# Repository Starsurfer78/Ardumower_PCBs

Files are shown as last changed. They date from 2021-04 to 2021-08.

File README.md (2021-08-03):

DIY Robot Lawn Mower Community: https://www.diy-robot-lawn-mower.com/

# Simple Ardumower_PCBs

If you want to buy a Board, you can send me an E-Mail: info@projekt-heimwerken.de

# Simple MainPCB only for Arduino DUE or Grand Central

New Board Design. All Pins from Software are now on the PCB. 
Supports 4 Motor Driver for Mowing.
Only a few Electronic Parts are needed. 
- JST-XH Connectors
- Screw Terminal 5.04mm
- Resistors
- Pin Header Connector 2.54mm
- Active Buzzer
- LED
- Jumper

Tested with MC33926 motor driver. Brushless Motordriver did not work at the Moment with Azuritber.

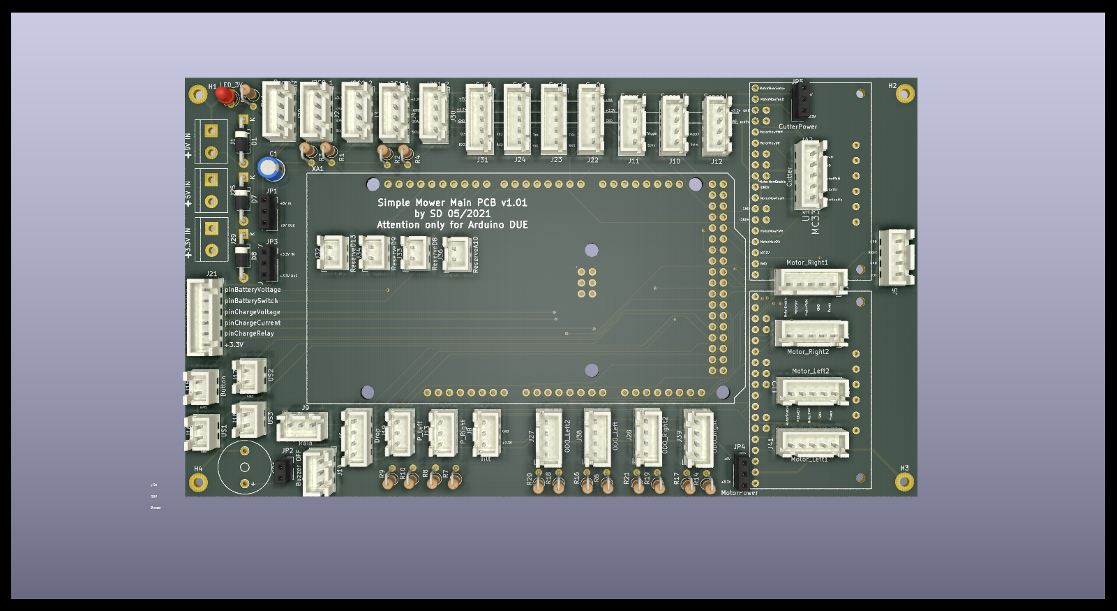
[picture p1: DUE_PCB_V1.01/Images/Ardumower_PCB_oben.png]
Vorschau Due PCB


# Power PCB for Simple MainPCB

The charging board and the power supply for the motors are on a separate board.

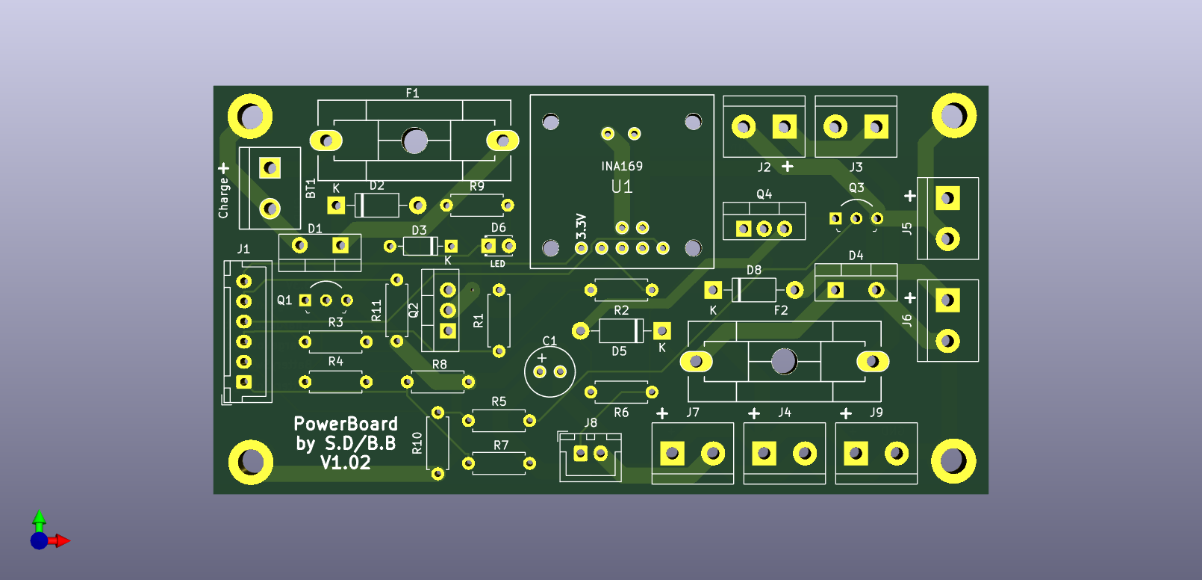
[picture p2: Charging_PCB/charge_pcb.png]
Vorschau Charging Board


Should also fit into small housings.

Use it at your own Risk.

Projekt: https://forum.ardumower.de/

Software Azuritber: https://github.com/Boilevin/AzuritBer

Ardumower Original Software: https://github.com/Ardumower

Facebook Gruppe DIY Robot Lawn Mower: https://www.facebook.com/groups/319588508137220

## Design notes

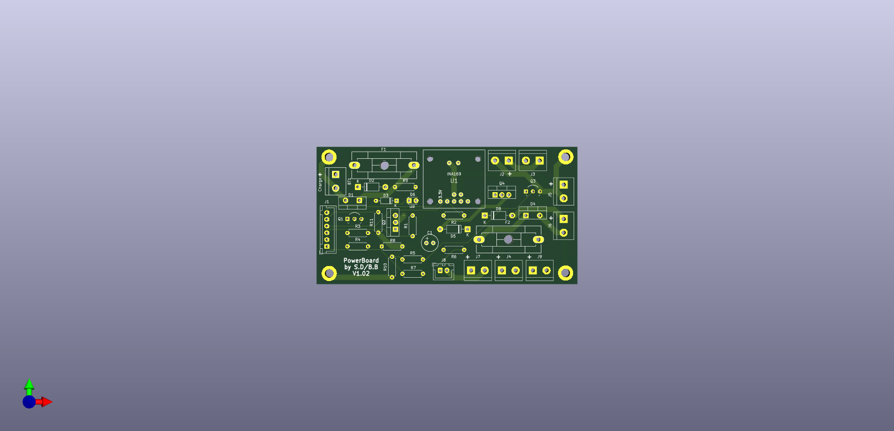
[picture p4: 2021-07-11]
Charging_PCB/charge_pcb_02.png

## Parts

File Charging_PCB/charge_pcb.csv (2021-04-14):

ID | Bezeichner | Gehäuse | Stückzahl | Bezeichnung | Anbieter und Referenz
1 | J3 | TerminalBlock_bornier-2_P5.08mm | 1 | Power Switch
2 | H2,H4,H3,H1 | MountingHole_3.2mm_M3_DIN965_Pad_TopBottom | 4 | MountingHole_Pad
3 | D6 | LED_D1.8mm_W3.3mm_H2.4mm | 1 | Station LED
4 | R9 | R_Axial_DIN0207_L6.3mm_D2.5mm_P7.62mm_Horizontal | 1 | 4.7kO
5 | U1 | INA169_mit_Pinnummern | 1 | ACS712
6 | R8,R2 | R_Axial_DIN0207_L6.3mm_D2.5mm_P7.62mm_Horizontal | 2 | 10k
7 | R7,R1 | R_Axial_DIN0207_L6.3mm_D2.5mm_P7.62mm_Horizontal | 2 | 100k
8 | R6,R5,R4,R3 | R_Axial_DIN0207_L6.3mm_D2.5mm_P7.62mm_Horizontal | 4 | 4k7
9 | Q4,Q2 | SIPAK-1EP_Horizontal_TabDown | 2 | IRLB 8721
10 | Q3,Q1 | TO-92-3_Formed_Leads | 2 | BC547C
11 | J7 | TerminalBlock_bornier-2_P5.08mm | 1 | Motor_Right
12 | J6 | TerminalBlock_bornier-2_P5.08mm | 1 | Motor_Cutter
13 | J5 | TerminalBlock_bornier-2_P5.08mm | 1 | Motor_Left
14 | J4 | TerminalBlock_bornier-2_P5.08mm | 1 | 24V Out
15 | J2 | TerminalBlock_bornier-2_P5.08mm | 1 | Battery
16 | J1 | PinHeader_1x06_P2.54mm_Vertical | 1 | PCB_1
17 | F2 | Fuseholder_Reichelt_PL112000 | 1 | 10A
18 | F1 | Fuseholder_Reichelt_PL112000 | 1 | 5A
19 | D5,D2 | D_DO-41_SOD81_P10.16mm_Horizontal | 2 | SB1240
20 | D4,D1 | TO-220-2_Vertical | 2 | MBR1045
21 | D3 | D_DO-35_SOD27_P7.62mm_Horizontal | 1 | 1N4148
22 | C1 | Elko_vert_11.2x6.3mm_RM2.5 | 1 | 100uF
23 | BT1 | Anschlussklemme_2P_RM5,08 | 1 | Charge

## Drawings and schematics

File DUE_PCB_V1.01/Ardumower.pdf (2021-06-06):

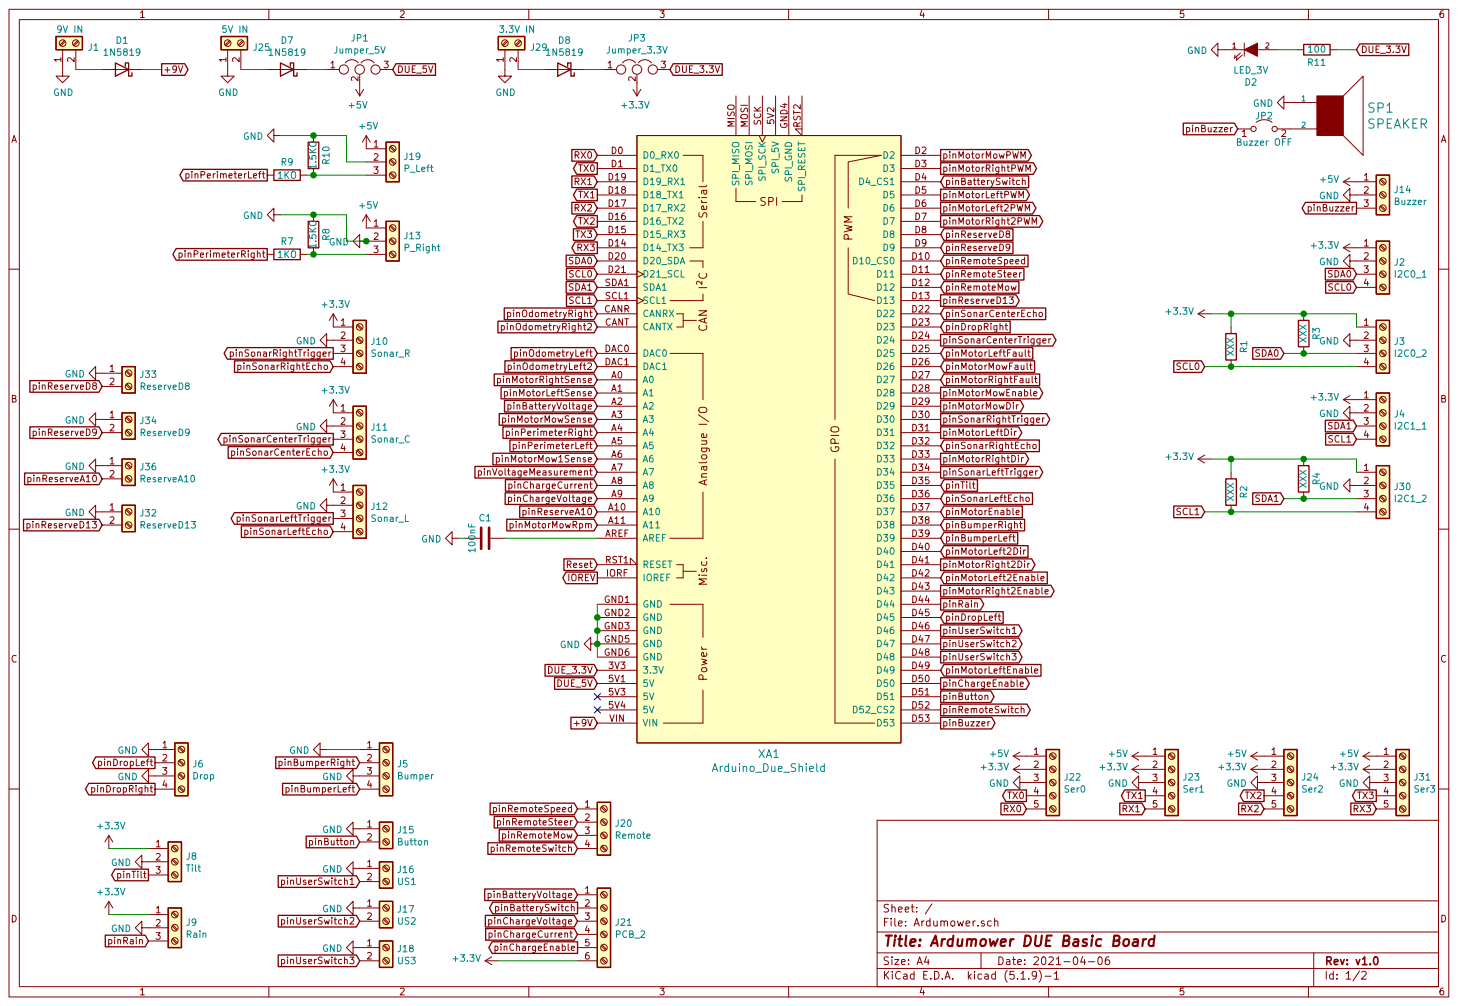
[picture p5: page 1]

File: Ardumower.sch Sheet: /
Id: 1/2 Title: Ardumower DUE Basic Board

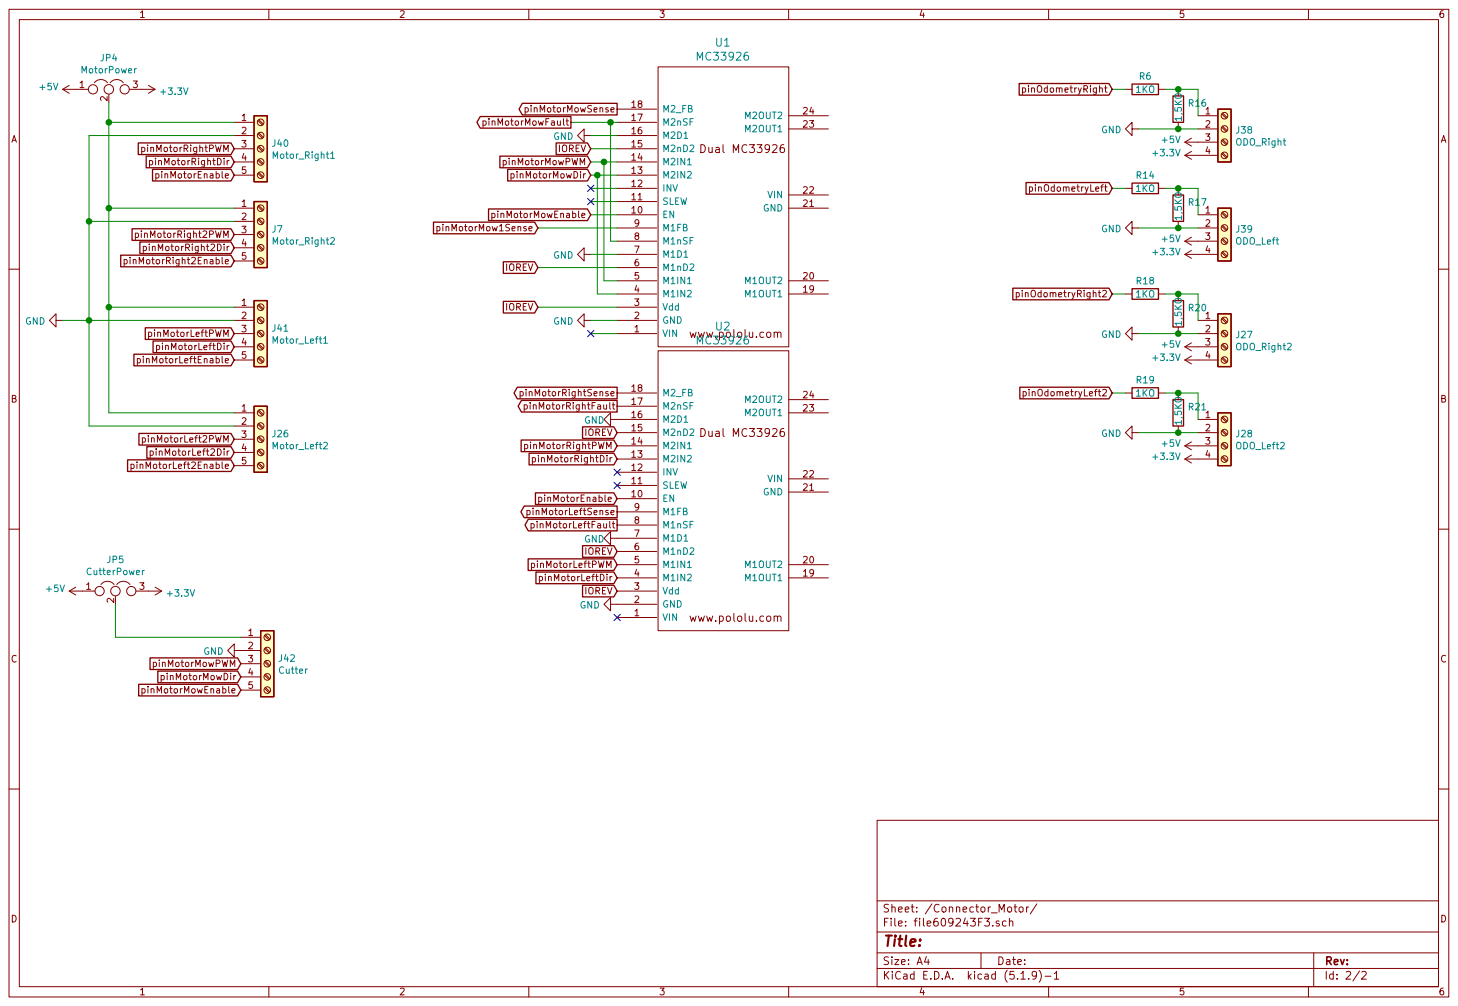
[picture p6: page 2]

J38 ODO_Right GND
GND GND
IOREV

Id: 2/2 Title: File: file609243F3.sch Sheet: /Connector_Motor/

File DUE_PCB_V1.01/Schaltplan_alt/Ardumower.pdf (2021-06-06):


File: Ardumower.sch Sheet: /
Id: 1/2 Title: Ardumower DUE Basic Board

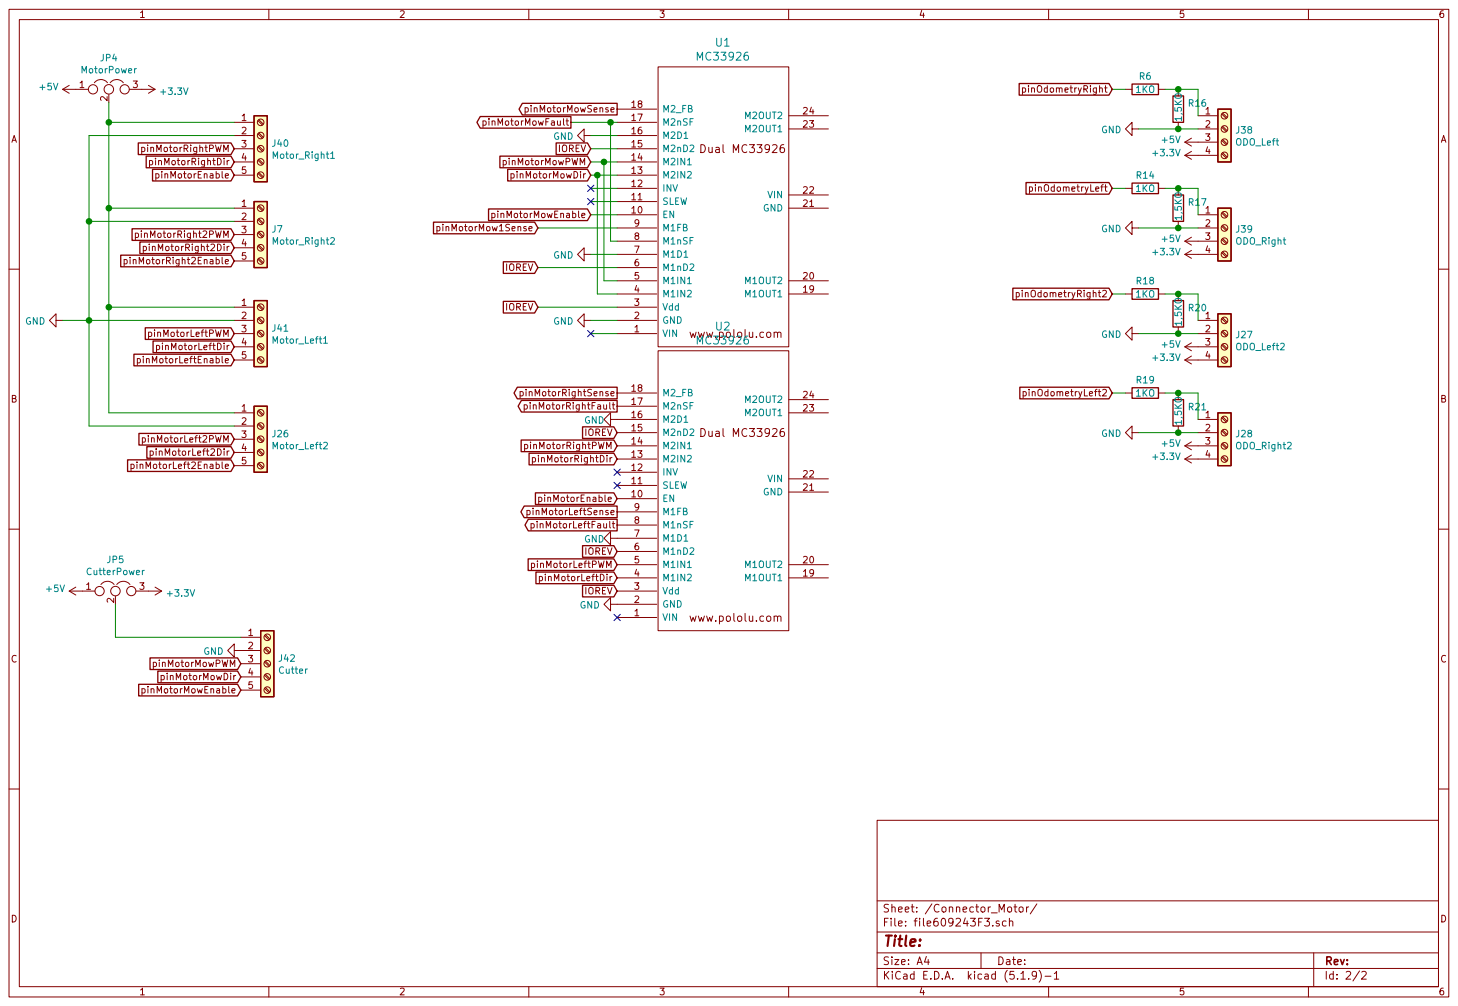
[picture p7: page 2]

J38 ODO_Left GND
GND GND
IOREV

Id: 2/2 Title: File: file609243F3.sch Sheet: /Connector_Motor/

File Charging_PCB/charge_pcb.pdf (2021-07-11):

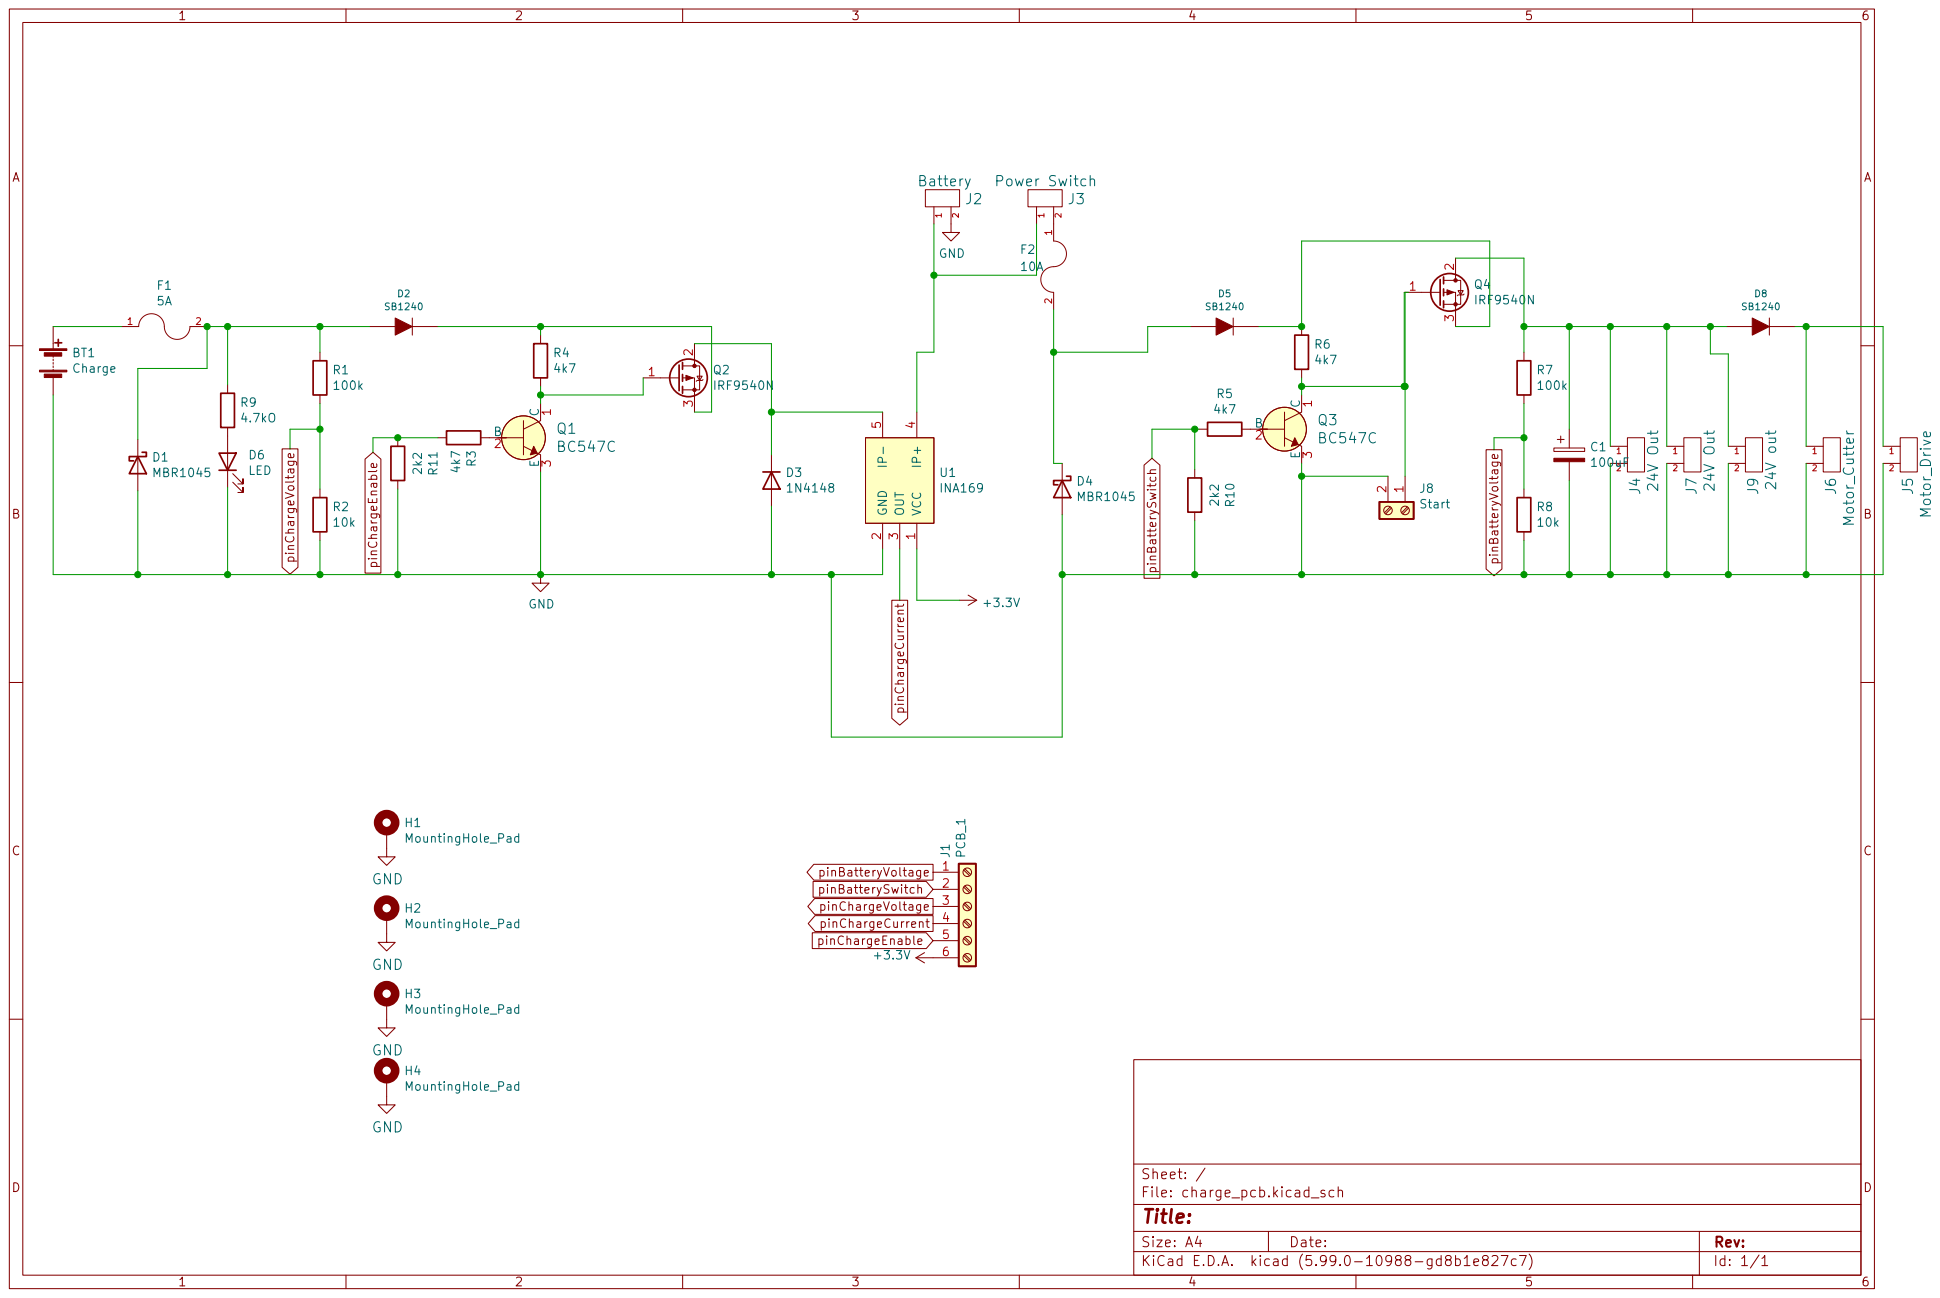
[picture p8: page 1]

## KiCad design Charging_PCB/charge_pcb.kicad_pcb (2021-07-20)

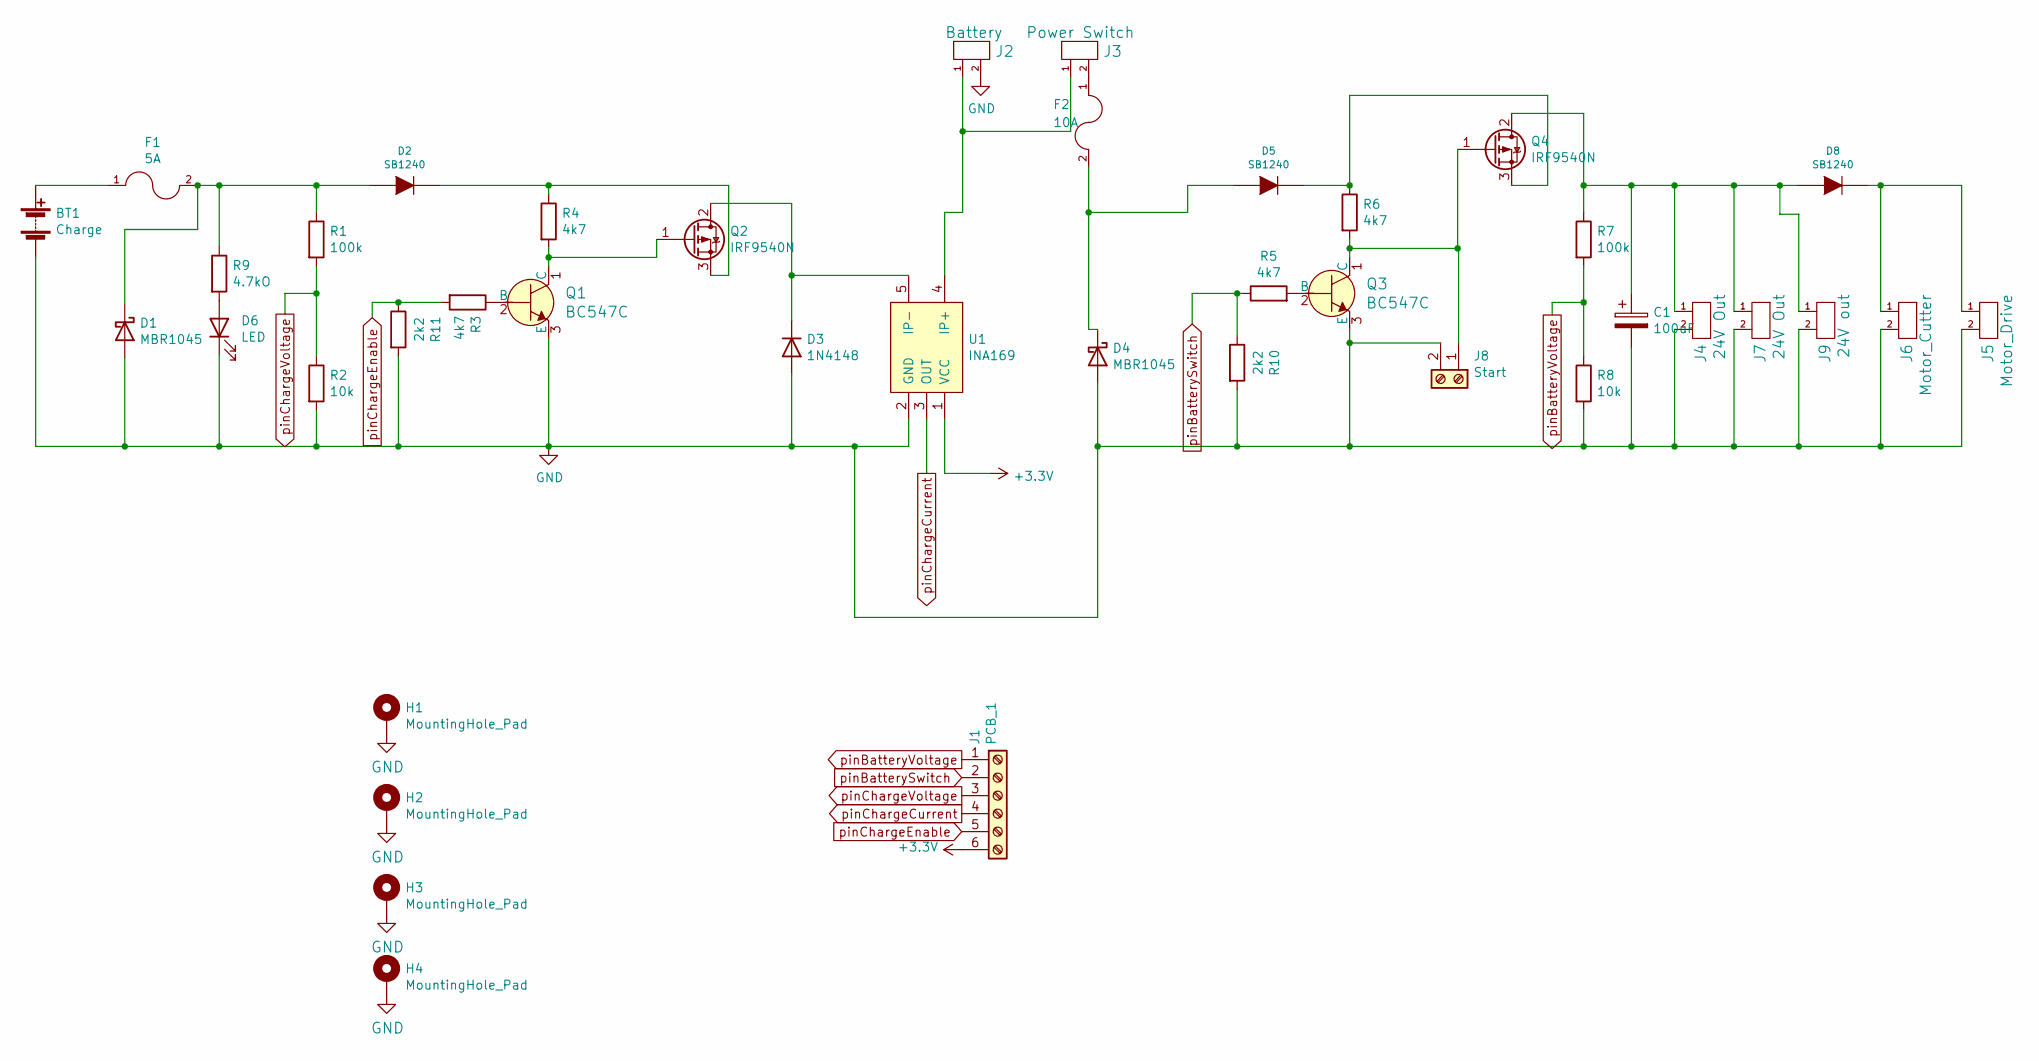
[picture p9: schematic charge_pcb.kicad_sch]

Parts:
BT1: Charge; Anschlussklemme_2P_RM5,08
C1: 100uF; Elko_vert_11.2x6.3mm_RM2.5
D1, D4: MBR1045; TO-220-2_Vertical
D2, D5, D8: SB1240; D_DO-41_SOD81_P10.16mm_Horizontal
D3: 1N4148; D_DO-35_SOD27_P7.62mm_Horizontal
D6: LED; LED_D1.8mm_W3.3mm_H2.4mm
F1: 5A; Fuseholder_Reichelt_PL112000
F2: 10A; Fuseholder_Reichelt_PL112000
H1, H2, H3, H4: MountingHole_Pad; MountingHole_3.2mm_M3_DIN965_Pad_TopBottom
J1: PCB_1; JST_XH_B6B-XH-A_1x06_P2.50mm_Vertical
J2: Battery; TerminalBlock_bornier-2_P5.08mm
J3: Power Switch; TerminalBlock_bornier-2_P5.08mm
J4, J7: 24V Out; TerminalBlock_bornier-2_P5.08mm
J5: Motor_Drive; TerminalBlock_bornier-2_P5.08mm
J6: Motor_Cutter; TerminalBlock_bornier-2_P5.08mm
J8: Start; JST_XH_B2B-XH-A_1x02_P2.50mm_Vertical
J9: 24V out; TerminalBlock_bornier-2_P5.08mm
Q1, Q3: BC547C; TO-92-3_Formed_Leads; MPN BC548BTA; Digi-Key_PN BC548BTACT-ND
Q2, Q4: IRF9540N; TO-220-3_Vertical
R1, R7: 100k; R_Axial_DIN0207_L6.3mm_D2.5mm_P7.62mm_Horizontal
R2, R8: 10k; R_Axial_DIN0207_L6.3mm_D2.5mm_P7.62mm_Horizontal
R3, R4, R5, R6: 4k7; R_Axial_DIN0207_L6.3mm_D2.5mm_P7.62mm_Horizontal
R9: 4.7kO; R_Axial_DIN0207_L6.3mm_D2.5mm_P7.62mm_Horizontal
R10, R11: 2k2; R_Axial_DIN0207_L6.3mm_D2.5mm_P7.62mm_Horizontal
U1: INA169; INA169_mit_Pinnummern

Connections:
+3V3: J1.6, U1.1 (VCC)
GND: BT1.2 (-), C1.2, D1.2 (A), D3.2 (A), D4.2 (A), D6.1 (K), H1.1, H2.1, H3.1, H4.1, J2.2, J4.2, J5.2, J6.2, J7.2, J8.2, J9.2, Q1.3 (E), Q3.3 (E), R2.2, R8.2, R10.2, R11.2, U1.2 (GND)
unnamed: BT1.1 (+), F1.1
unnamed: C1.1, D8.1 (A), J4.1, J7.1, J9.1, Q4.2 (D), R7.1
unnamed: D1.1 (K), D2.1 (A), F1.2, R1.1, R9.1
unnamed: D2.2 (K), Q2.3 (S), R4.1
unnamed: D3.1 (K), Q2.2 (D), U1.5 (IP-)
unnamed: D4.1 (K), D5.1 (A), F2.2
unnamed: D5.2 (K), Q4.3 (S), R6.1
unnamed: D6.2 (A), R9.2
unnamed: D8.2 (K), J5.1, J6.1
unnamed: F2.1, J3.2
unnamed: J2.1, J3.1, U1.4 (IP+)
unnamed: J8.1, Q3.1 (C), Q4.1 (G), R6.2
unnamed: Q1.1 (C), Q2.1 (G), R4.2
unnamed: Q1.2 (B), R3.1
unnamed: Q3.2 (B), R5.2
pinBatterySwitch: J1.2, R5.1, R10.1
pinBatteryVoltage: J1.1, R7.2, R8.1
pinChargeCurrent: J1.4, U1.3 (OUT)
pinChargeEnable: J1.5, R3.2, R11.1
pinChargeVoltage: J1.3, R1.2, R2.1

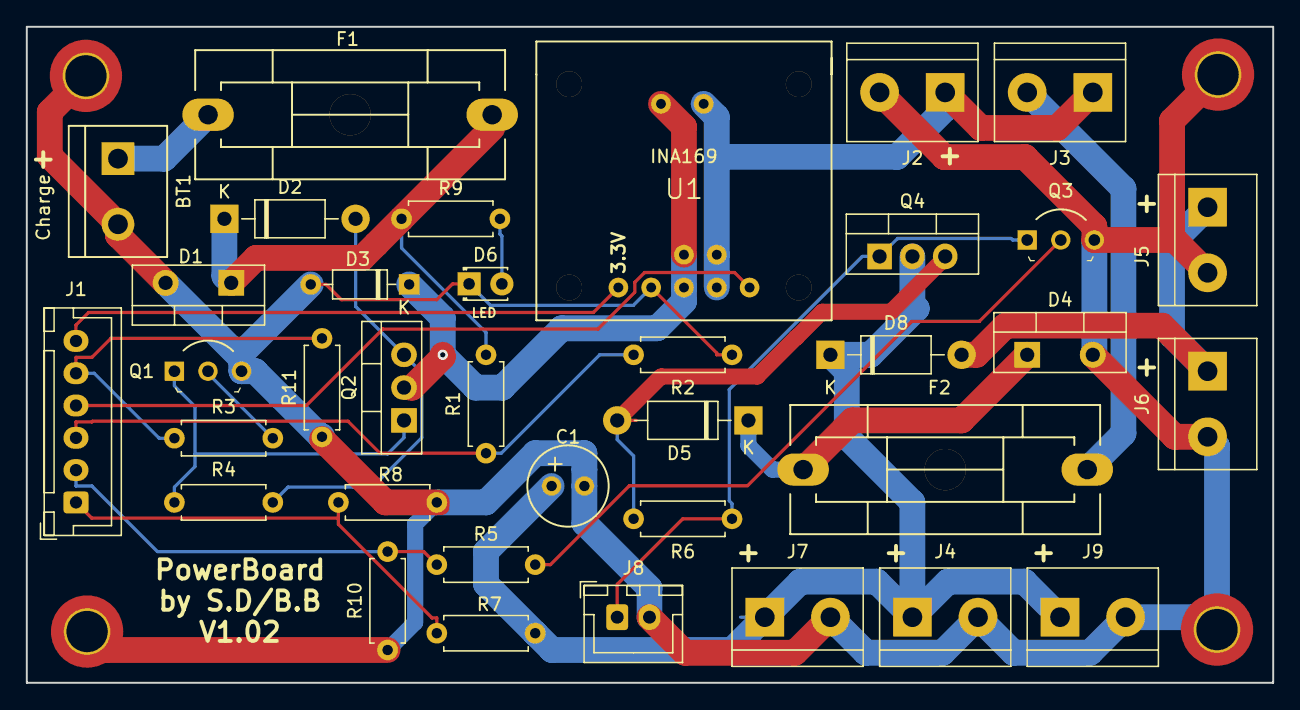
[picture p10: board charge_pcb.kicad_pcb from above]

Board: 2 copper layers, 96.5 x 50.8 mm, 40 parts (0 on the bottom side), 22 nets.

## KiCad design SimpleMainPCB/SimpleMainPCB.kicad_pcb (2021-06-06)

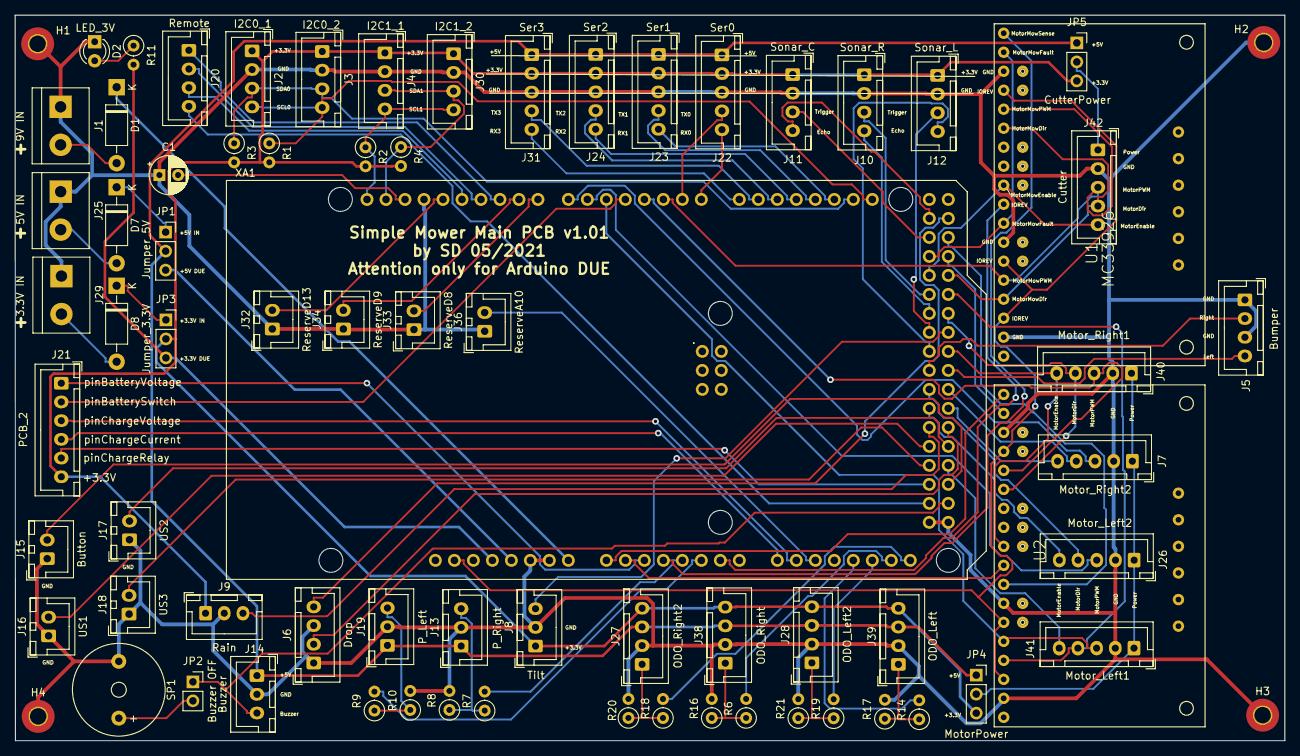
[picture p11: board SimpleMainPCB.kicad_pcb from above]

Board: 2 copper layers, 169.8 x 97.0 mm, 75 parts (0 on the bottom side), 93 nets.

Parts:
C1: 100nF; CP_Radial_D5.0mm_P2.50mm
D1, D7, D8: 1N5819; D_DO-41_SOD81_P10.16mm_Horizontal
D2: LED_3V; LED_D3.0mm
H1, H2, H3, H4: MountingHole_Pad; MountingHole_2.2mm_M2_Pad_TopBottom
J1: 9V IN; TerminalBlock_bornier-2_P5.08mm
J2: I2C0_1; JST_XH_B4B-XH-A_1x04_P2.50mm_Vertical
J3: I2C0_2; JST_XH_B4B-XH-A_1x04_P2.50mm_Vertical
J4: I2C1_1; JST_XH_B4B-XH-A_1x04_P2.50mm_Vertical
J5: Bumper; JST_XH_B4B-XH-A_1x04_P2.50mm_Vertical
J6: Drop; JST_XH_B4B-XH-A_1x04_P2.50mm_Vertical
J7: Motor_Right2; JST_XH_B5B-XH-A_1x05_P2.50mm_Vertical
J8: Tilt; JST_XH_B3B-XH-A_1x03_P2.50mm_Vertical
J9: Rain; JST_XH_B3B-XH-A_1x03_P2.50mm_Vertical
J10: Sonar_R; JST_XH_B4B-XH-A_1x04_P2.50mm_Vertical
J11: Sonar_C; JST_XH_B4B-XH-A_1x04_P2.50mm_Vertical
J12: Sonar_L; JST_XH_B4B-XH-A_1x04_P2.50mm_Vertical
J13: P_Right; JST_XH_B3B-XH-A_1x03_P2.50mm_Vertical
J14: Buzzer; JST_XH_B3B-XH-A_1x03_P2.50mm_Vertical
J15: Button; JST_XH_B2B-XH-A_1x02_P2.50mm_Vertical
J16: US1; JST_XH_B2B-XH-A_1x02_P2.50mm_Vertical
J17: US2; JST_XH_B2B-XH-A_1x02_P2.50mm_Vertical
J18: US3; JST_XH_B2B-XH-A_1x02_P2.50mm_Vertical
J19: P_Left; JST_XH_B3B-XH-A_1x03_P2.50mm_Vertical
J20: Remote; JST_XH_B4B-XH-A_1x04_P2.50mm_Vertical
J21: PCB_2; JST_XH_B6B-XH-A_1x06_P2.50mm_Vertical
J22: Ser0; JST_XH_B5B-XH-A_1x05_P2.50mm_Vertical
J23: Ser1; JST_XH_B5B-XH-A_1x05_P2.50mm_Vertical
J24: Ser2; JST_XH_B5B-XH-A_1x05_P2.50mm_Vertical
J25: 5V IN; TerminalBlock_bornier-2_P5.08mm
J26: Motor_Left2; JST_XH_B5B-XH-A_1x05_P2.50mm_Vertical
J27: ODO_Right2; JST_XH_B4B-XH-A_1x04_P2.50mm_Vertical
J28: ODO_Left2; JST_XH_B4B-XH-A_1x04_P2.50mm_Vertical
J29: 3.3V IN; TerminalBlock_bornier-2_P5.08mm
J30: I2C1_2; JST_XH_B4B-XH-A_1x04_P2.50mm_Vertical
J31: Ser3; JST_XH_B5B-XH-A_1x05_P2.50mm_Vertical
J32: ReserveD13; JST_XH_B2B-XH-A_1x02_P2.50mm_Vertical
J33: ReserveD8; JST_XH_B2B-XH-A_1x02_P2.50mm_Vertical
J34: ReserveD9; JST_XH_B2B-XH-A_1x02_P2.50mm_Vertical
J36: ReserveA10; JST_XH_B2B-XH-A_1x02_P2.50mm_Vertical
J38: ODO_Right; JST_XH_B4B-XH-A_1x04_P2.50mm_Vertical
J39: ODO_Left; JST_XH_B4B-XH-A_1x04_P2.50mm_Vertical
J40: Motor_Right1; JST_XH_B5B-XH-A_1x05_P2.50mm_Vertical
J41: Motor_Left1; JST_XH_B5B-XH-A_1x05_P2.50mm_Vertical
J42: Cutter; JST_XH_B5B-XH-A_1x05_P2.50mm_Vertical
JP1: Jumper_5V; PinSocket_1x03_P2.54mm_Vertical
JP2: Buzzer OFF; PinSocket_1x02_P2.54mm_Vertical
JP3: Jumper_3.3V; PinSocket_1x03_P2.54mm_Vertical
JP4: MotorPower; PinSocket_1x03_P2.54mm_Vertical
JP5: CutterPower; PinSocket_1x03_P2.54mm_Vertical
R1, R2, R3, R4: XXX; R_Axial_DIN0207_L6.3mm_D2.5mm_P2.54mm_Vertical
R6, R7, R9, R14, R18, R19: 1KO; R_Axial_DIN0207_L6.3mm_D2.5mm_P2.54mm_Vertical
R8, R10: 1.5KO; R_Axial_DIN0207_L6.3mm_D2.5mm_P2.54mm_Vertical
R11: 100; R_Axial_DIN0207_L6.3mm_D2.5mm_P2.54mm_Vertical
R16, R17, R20, R21: 1,5KO; R_Axial_DIN0207_L6.3mm_D2.5mm_P2.54mm_Vertical
SP1: SPEAKER; Buzzer_12x9.5RM7.6
U1, U2: MC33926; MC_33926_31polig_mit_Bohrloch_neue_Masse
XA1: Arduino_Due_Shield

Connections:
+3V3: J2.1, J3.1, J4.1, J8.1, J9.1, J10.1, J11.1, J12.1, J21.6, J22.2, J23.2, J24.2, J27.4, J28.4, J30.1, J31.2, J38.4, J39.4, JP3.2, JP4.3, JP5.3, R1.2, R2.2, R3.2, R4.2
+5V: J13.1, J14.1, J19.1, J22.1, J23.1, J24.1, J27.3, J28.3, J31.1, J38.3, J39.3, JP1.2, JP4.1, JP5.1
+9V: D1.1, XA1.VIN
DUE_3.3V: JP3.3, R11.2, XA1.3V3
DUE_5V: JP1.3, XA1.5V1
GND: C1.1, D2.1, H1.1, H2.1, H3.1, H4.1, J1.1, J2.2, J3.2, J4.2, J5.1, J5.3, J6.1, J6.3, J7.2, J8.2, J9.2, J10.2, J11.2, J12.2, J13.2, J14.2, J15.1, J16.1, J17.1, J18.1, J19.2, J22.3, J23.3, J24.3, J25.1, J26.2, J27.2, J28.2, J29.1, J30.2, J31.3, J32.1, J33.1, J34.1, J36.1, J38.2, J39.2, J40.2, J41.2, J42.2, R8.2, R10.2, R16.2, R17.2, R20.2, R21.2, SP1.1, U1.2, U1.7, U1.16, U2.2, U2.7, U2.16, XA1.GND1, XA1.GND2, XA1.GND3, XA1.GND5, XA1.GND6
IOREV: U1.3, U1.6, U1.15, U2.3, U2.6, U2.15, XA1.IORF
unnamed: C1.2, XA1.AREF
unnamed: D1.2, J1.2
unnamed: D2.2, R11.1
unnamed: D7.1, JP1.1
unnamed: D7.2, J25.2
unnamed: D8.1, JP3.1
unnamed: D8.2, J29.2
unnamed: J13.3, R7.1, R8.1
unnamed: J19.3, R9.1, R10.1
unnamed: J7.1, J26.1, J40.1, J41.1, JP4.2
unnamed: J27.1, R18.1, R20.1
unnamed: J28.1, R19.1, R21.1
unnamed: J38.1, R6.1, R16.1
unnamed: J39.1, R14.1, R17.1
unnamed: J42.1, JP5.2
unnamed: JP2.2, SP1.2
RX0: J22.5, XA1.D0
RX1: J23.5, XA1.D19
RX2: J24.5, XA1.D17
RX3: J31.5, XA1.D14
SCL0: J2.4, J3.4, R1.1, XA1.D21
SCL1: J4.4, J30.4, R2.1, XA1.SCL1
SDA0: J2.3, J3.3, R3.1, XA1.D20
SDA1: J4.3, J30.3, R4.1, XA1.SDA1
TX0: J22.4, XA1.D1
TX1: J23.4, XA1.D18
TX2: J24.4, XA1.D16
TX3: J31.4, XA1.D15
pinBatterySwitch: J21.2, XA1.D4
pinBatteryVoltage: J21.1, XA1.A2
pinBumperLeft: J5.4, XA1.D39
pinBumperRight: J5.2, XA1.D38
pinButton: J15.2, XA1.D51
pinBuzzer: J14.3, JP2.1, XA1.D53
pinChargeCurrent: J21.4, XA1.A8
pinChargeEnable: J21.5, XA1.D50
pinChargeVoltage: J21.3, XA1.A9
pinDropLeft: J6.2, XA1.D45
pinDropRight: J6.4, XA1.D23
pinMotorEnable: J40.5, U2.10, XA1.D37
pinMotorLeft2Dir: J26.4, XA1.D40
pinMotorLeft2Enable: J26.5, XA1.D42
pinMotorLeft2PWM: J26.3, XA1.D6
pinMotorLeftDir: J41.4, U2.4, XA1.D31
pinMotorLeftEnable: J41.5, XA1.D49
pinMotorLeftFault: U2.8, XA1.D25
pinMotorLeftPWM: J41.3, U2.5, XA1.D5
pinMotorLeftSense: U2.9, XA1.A1
pinMotorMow1Sense: U1.9, XA1.A6
pinMotorMowDir: J42.4, U1.4, U1.13, XA1.D29
pinMotorMowEnable: J42.5, U1.10, XA1.D28
pinMotorMowFault: U1.8, U1.17, XA1.D26
pinMotorMowPWM: J42.3, U1.5, U1.14, XA1.D2
pinMotorMowSense: U1.18, XA1.A3
pinMotorRight2Dir: J7.4, XA1.D41
pinMotorRight2Enable: J7.5, XA1.D43
pinMotorRight2PWM: J7.3, XA1.D7
pinMotorRightDir: J40.4, U2.13, XA1.D33
pinMotorRightFault: U2.17, XA1.D27
pinMotorRightPWM: J40.3, U2.14, XA1.D3
pinMotorRightSense: U2.18, XA1.A0
pinOdometryLeft: R14.2, XA1.DAC0
pinOdometryLeft2: R19.2, XA1.DAC1
pinOdometryRight: R6.2, XA1.CANR
pinOdometryRight2: R18.2, XA1.CANT
pinPerimeterLeft: R9.2, XA1.A5
pinPerimeterRight: R7.2, XA1.A4
pinRain: J9.3, XA1.D44
pinRemoteMow: J20.3, XA1.D12
pinRemoteSpeed: J20.1, XA1.D10
pinRemoteSteer: J20.2, XA1.D11
pinRemoteSwitch: J20.4, XA1.D52
pinReserveA10: J36.2, XA1.A10
pinReserveD8: J33.2, XA1.D8
pinReserveD9: J34.2, XA1.D9
pinReserveD13: J32.2, XA1.D13
pinSonarCenterEcho: J11.4, XA1.D22
pinSonarCenterTrigger: J11.3, XA1.D24
pinSonarLeftEcho: J12.4, XA1.D36
pinSonarLeftTrigger: J12.3, XA1.D34
pinSonarRightEcho: J10.4, XA1.D32
pinSonarRightTrigger: J10.3, XA1.D30
pinTilt: J8.3, XA1.D35
pinUserSwitch1: J16.2, XA1.D46
pinUserSwitch2: J17.2, XA1.D47
pinUserSwitch3: J18.2, XA1.D48

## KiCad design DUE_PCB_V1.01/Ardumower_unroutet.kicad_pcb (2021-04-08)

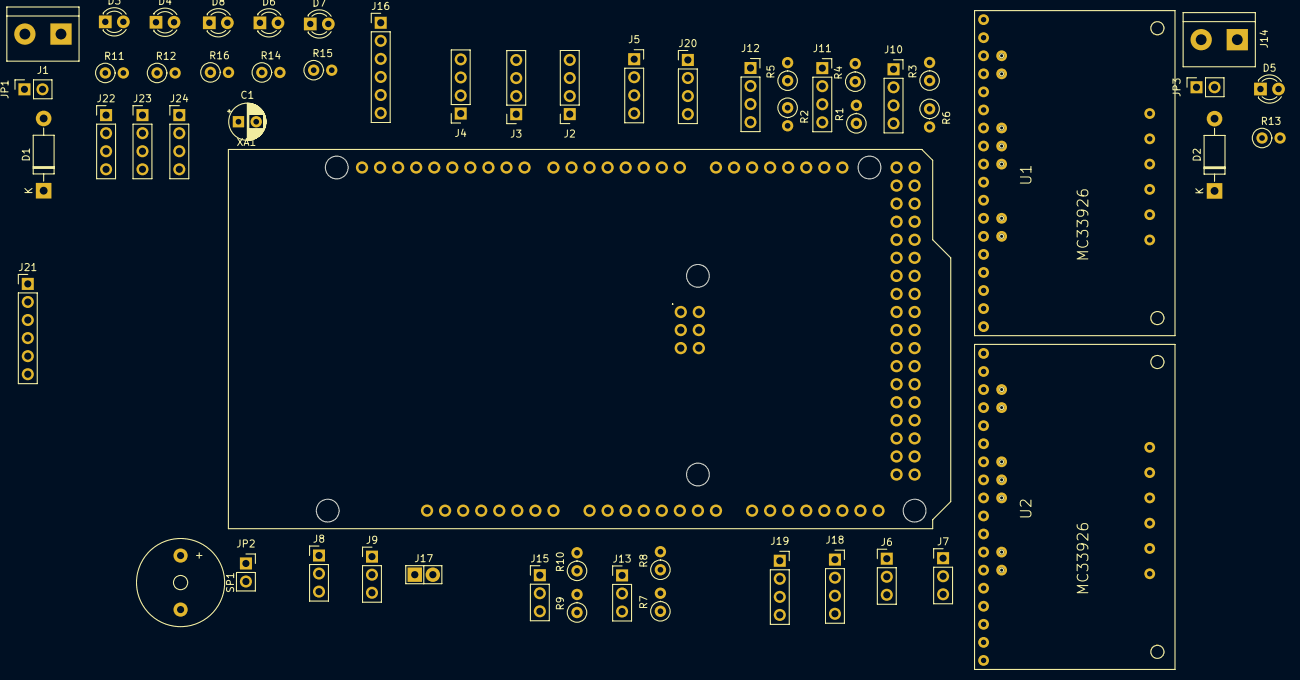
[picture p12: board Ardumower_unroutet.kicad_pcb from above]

Board: 2 copper layers, 56 parts (0 on the bottom side), 78 nets, no tracks yet.

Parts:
C1: 100nF; CP_Radial_D5.0mm_P2.50mm
D1, D2: 1N5819; D_DO-41_SOD81_P10.16mm_Horizontal
D3: LED_3V; LED_D3.0mm
D4: LED_5V; LED_D3.0mm
D5: LED_24V; LED_D3.0mm
D6: LED; LED_D3.0mm
D7: LED_Green; LED_D3.0mm
D8: LED_Red; LED_D3.0mm
J1: 9V IN; TerminalBlock_bornier-2_P5.08mm
J2: I2C_1; PinSocket_1x04_P2.54mm_Vertical
J3: I2C_2; PinSocket_1x04_P2.54mm_Vertical
J4: I2C_3; PinSocket_1x04_P2.54mm_Vertical
J5: Bumper; PinSocket_1x04_P2.54mm_Vertical
J6: Drop_Left; PinHeader_1x03_P2.54mm_Vertical
J7: Drop_Right; PinHeader_1x03_P2.54mm_Vertical
J8: Tilt; PinHeader_1x03_P2.54mm_Vertical
J9: Rain; PinHeader_1x03_P2.54mm_Vertical
J10: Sonar_R; PinSocket_1x04_P2.54mm_Vertical
J11: Sonar_C; PinSocket_1x04_P2.54mm_Vertical
J12: Sonar_L; PinSocket_1x04_P2.54mm_Vertical
J13: P_Right; PinHeader_1x03_P2.54mm_Vertical
J14: 24V IN; TerminalBlock_bornier-2_P5.08mm
J15: P_Left; PinHeader_1x03_P2.54mm_Vertical
J16: DS3231 RTC; PinHeader_1x06_P2.54mm_Vertical
J17: Button; Pin_Header_KK110_1x02_3D
J18: ODO_Right; PinSocket_1x04_P2.54mm_Vertical
J19: ODO_Left; PinSocket_1x04_P2.54mm_Vertical
J20: Remote; PinHeader_1x04_P2.54mm_Vertical
J21: PCB_2; PinHeader_1x06_P2.54mm_Vertical
J22: 3.3V; PinHeader_1x04_P2.54mm_Vertical
J23: GND; PinHeader_1x04_P2.54mm_Vertical
J24: RX & TX; PinHeader_1x04_P2.54mm_Vertical
JP1: 9V; PinSocket_1x02_P2.54mm_Vertical
JP2: Buzzer OFF; PinSocket_1x02_P2.54mm_Vertical
JP3: 24V; PinSocket_1x02_P2.54mm_Vertical
R1, R2, R3, R7, R9: 1KO; R_Axial_DIN0207_L6.3mm_D2.5mm_P2.54mm_Vertical
R4, R5, R6: 2KO; R_Axial_DIN0207_L6.3mm_D2.5mm_P2.54mm_Vertical
R8, R10: 1.5KO; R_Axial_DIN0207_L6.3mm_D2.5mm_P2.54mm_Vertical
R11, R14, R15, R16: 100; R_Axial_DIN0207_L6.3mm_D2.5mm_P2.54mm_Vertical
R12: 220; R_Axial_DIN0207_L6.3mm_D2.5mm_P2.54mm_Vertical
R13: 1K5; R_Axial_DIN0207_L6.3mm_D2.5mm_P2.54mm_Vertical
SP1: SPEAKER; Buzzer_12x9.5RM7.6
U1, U2: MC33926; MC_33926_31polig_mit_Bohrloch_neue_Masse
XA1: Arduino_Due_Shield

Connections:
+3V3: J2.1, J3.1, J4.1, J6.1, J7.1, J8.1, J9.1, J16.5, J22.1, J22.2, J22.3, J22.4, R11.2, XA1.3V3
+5V: J10.1, J11.1, J12.1, J13.1, J15.1, J18.1, J19.1, R12.2, XA1.5V1
+9V: D1.1, XA1.VIN
+24V: D2.1, R13.2, U1.22, U2.22
GND: C1.1, D3.1, D4.1, D5.1, D6.1, D7.1, D8.1, J1.1, J2.2, J3.2, J4.2, J5.1, J5.3, J6.2, J7.2, J8.2, J9.2, J10.2, J11.2, J12.2, J13.2, J14.1, J15.2, J16.6, J17.1, J18.2, J19.2, J23.1, J23.2, J23.3, J23.4, R4.2, R5.2, R6.2, R8.2, R10.2, SP1.1, U1.2, U1.7, U1.16, U1.21, U2.2, U2.7, U2.16, U2.21, XA1.GND1, XA1.GND2, XA1.GND3, XA1.GND5, XA1.GND6
IOREV: U1.3, U1.6, U1.9, U1.15, U2.3, U2.6, U2.15, XA1.IORF
unnamed: C1.2, XA1.AREF
unnamed: D1.2, JP1.2
unnamed: D2.2, JP3.2
unnamed: D3.2, R11.1
unnamed: D4.2, R12.1
unnamed: D5.2, R13.1
unnamed: D6.2, R14.2
unnamed: D7.2, R15.2
unnamed: D8.2, R16.2
unnamed: J1.2, JP1.1
unnamed: J10.3, R3.1, R6.1
unnamed: J11.3, R1.1, R4.1
unnamed: J12.3, R2.1, R5.1
unnamed: J13.3, R7.1, R8.1
unnamed: J14.2, JP3.1
unnamed: J15.3, R9.1, R10.1
unnamed: JP2.2, SP1.2
RX1: J24.2, XA1.D19
RX2: J24.4, XA1.D17
SCL0: J2.4, J3.4, XA1.D21
SCL1: J4.4, J16.3, XA1.SCL1
SDA0: J2.3, J3.3, XA1.D20
SDA1: J4.3, J16.4, XA1.SDA1
TX1: J24.1, XA1.D18
TX2: J24.3, XA1.D16
pinBatterySwitch: J21.2, XA1.D4
pinBatteryVoltage: J21.1, XA1.A2
pinBumperLeft: J5.4, XA1.D39
pinBumperRight: J5.2, XA1.D38
pinButton: J17.2, XA1.D51
pinBuzzer: JP2.1, XA1.D53
pinChargeCurrent: J21.4, XA1.A8
pinChargeRelay: J21.5, XA1.D50
pinChargeVoltage: J21.3, XA1.A9
pinDropLeft: J6.3, XA1.D45
pinDropRight: J7.3, XA1.D23
pinGreenLED: R15.1, XA1.D6
pinLED: R14.1, XA1.D13
pinMotorEnable: U2.10, XA1.D37
pinMotorLeftDir: U2.4, XA1.D31
pinMotorLeftFault: U2.8, XA1.D25
pinMotorLeftPWM: U2.5, XA1.D5
pinMotorLeftSense: U2.9, XA1.A1
pinMotorMowDir: U1.4, U1.13, XA1.D29
pinMotorMowEnable: U1.10, XA1.D28
pinMotorMowFault: U1.8, U1.17, XA1.D26
pinMotorMowPWM: U1.5, U1.14, XA1.D2
pinMotorMowSense: U1.18, XA1.A3
pinMotorRightDir: U2.13, XA1.D33
pinMotorRightFault: U2.17, XA1.D27
pinMotorRightPWM: U2.14, XA1.D3
pinMotorRightSense: U2.18, XA1.A0
pinOdometryLeft: J19.3, XA1.DAC0
pinOdometryLeft2: J19.4, XA1.DAC1
pinOdometryRight: J18.3, XA1.CANR
pinOdometryRight2: J18.4, XA1.CANT
pinPerimeterLeft: R9.2, XA1.A5
pinPerimeterRight: R7.2, XA1.A4
pinRain: J9.3, XA1.D44
pinRedLED: R16.1, XA1.D7
pinRemoteMow: J20.3, XA1.D12
pinRemoteSpeed: J20.1, XA1.D10
pinRemoteSteer: J20.2, XA1.D11
pinRemoteSwitch: J20.4, XA1.D52
pinSonarCenterEcho: J11.4, XA1.D22
pinSonarCenterTrigger: R1.2, XA1.D24
pinSonarLeftEcho: J12.4, XA1.D36
pinSonarLeftTrigger: R2.2, XA1.D34
pinSonarRightEcho: J10.4, XA1.D32
pinSonarRightTrigger: R3.2, XA1.D30
pinTilt: J8.3, XA1.D35
pinVoltageMeasurement: J21.6, XA1.A7

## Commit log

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2021-04-08 Starsurfer78
    Sorting the Footprints on PCB
    [Ardumower.kicad_pcb, file609243F3.sch]
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2021-04-11 Change Name of Mosfet
    [charge_pcb.kicad_pcb, charge_pcb.sch]
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2021-05-04 Add Power Connector for 5V and 3.3V
    [Ardumower.kicad_pcb, Ardumower.sch, file609243F3.sch]
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2021-05-06 Ad new RX TX Connector and some other improvements
    [Ardumower.kicad_pcb, Ardumower.sch]
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2021-05-07 Change Jumper for Power Source
    Change Screw Terminal for 5V/3.3V to jumper.
    [Ardumower.kicad_pcb, Ardumower.sch]
2021-05-07 Change LED Power Source
    Change the Power Source from the LED_5V and LED_3.3V
    [Ardumower.kicad_pcb, Ardumower.sch]
2021-05-07 Change D6 and D7
    Add Description for PIN D6 and D7 to pinFrontMotorLeft and pinFrontMotorRight
    [Ardumower.kicad_pcb, Ardumower.sch, file609243F3.sch]
2021-05-07 Rename Pins
    Rename pinFrontMotorLeft to pinMotorLeft2PWM and pinFrontMotorRight to pinMotorRight2PWM
    [Ardumower.sch, file609243F3.sch]
2021-05-07 Add new Connectors for 4 Mow Motors and Odometrie
    Add new Connectors for 4 Mow Motors and Odometrie
    [Ardumower.kicad_pcb, file609243F3.sch]
2021-05-07 Add new Motor Schematic
    Add new Motor Schematic
    [Ardumower.kicad_pcb, file609243F3.sch]
2021-05-08 Remove Lawn Sense Pins
    Remove Lawn Sense Pins and add pinMotorLeft2Dir and pinMotorRight2Dir
    [Ardumower.sch, file609243F3.sch]
2021-05-08 Remove Resistors
    Remove R8, R9 and R13
    [Ardumower.sch]
2021-05-09 Motor Connector correctly named
    [file609243F3.sch]
2021-05-09 Rename Pins
    Rename ReservePinA10 to pinMotorLeftSense2
    [Ardumower.kicad_pcb, Ardumower.sch]
2021-05-09 Add I2C Pullup
    Add i2c Pullup to J1 & J3
    [Ardumower.kicad_pcb, Ardumower.sch]
2021-05-09 Update J30 and J32
    [Ardumower.sch]
2021-05-10 v102
    I have paste my work on the v1.02 hope it's work
    [Ardumower.dsn, Ardumower.kicad_pcb, Ardumower.sch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]
2021-05-11 Start ro add Bernard changes from 1.02
    [Ardumower.kicad_pcb, Ardumower.sch, file609243F3.sch]
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2021-05-12 Add Reserve Pin Connectors
    [Ardumower.kicad_pcb, Ardumower.sch]
2021-05-12 Change Pin Header to JST
    Change Pin Header to JST and sort them on the PCB
    [Ardumower.kicad_pcb, Ardumower.sch, file609243F3.sch]
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2021-05-13 Add Power Source
    Add Power Source for 5V & 3.3V
    [Ardumower.sch]
2021-05-13 Remove Sonar Resistors
    Remove Sonar Resistors and change Power Source to 3.3V
    [Ardumower.sch]
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2021-05-13 Add Pullup to I2C
    [Ardumower.sch]
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2021-05-13 Rename GPS_TX & GPS_RX to RX3 & TX3
    [Ardumower.sch]
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2021-05-13 Add Footprint for Ser0-Ser3
    [Ardumower.sch]
2021-05-13 Remove 2x4 Motor Pin Connectors
    [Ardumower.kicad_pcb, file609243F3.sch]
2021-05-13 Add Connector 24V for Motor & Cutter
    [file609243F3.sch]
2021-05-13 Sort Connectors on PCB
    [Ardumower.kicad_pcb]
2021-05-13 Add Pin Description on PCB
    [Ardumower.kicad_pcb, Ardumower.sch, file609243F3.sch]
2021-05-13 Add Zener Diode
    3.3 V zener diode to clamp the current sense output voltage to a maximum of ~3.3 V
    [Ardumower.kicad_pcb, file609243F3.sch]
2021-05-13 Add PCB Pin Description
    [Ardumower.kicad_pcb]
2021-05-14 Ad Odometrie Connector without Voltage Divider
    [file609243F3.sch]
2021-05-14 Add Voltage Divider to ODO
    [Ardumower.kicad_pcb, Ardumower.sch, file609243F3.sch]
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2021-05-15 Sorting Connectors on PCB
    [Ardumower.kicad_pcb, Ardumower_test.dsn]
2021-05-16 Change direction from i2c Pins
    Change direction from i2c Pins to pass with other pins direction
    [Ardumower.kicad_pcb]
2021-05-16 Add Motor Connectors
    Add Default Motor Connectors and reorder Ser0-Ser3
    [Ardumower.kicad_pcb, Ardumower.sch, file609243F3.sch]
2021-05-16 Change PCB Pin Description for Ser0-Ser3
    [Ardumower.kicad_pcb]
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2021-05-16 Small changes in Line Traces
    [Ardumower.kicad_pcb]
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2021-05-16 Small Changes
    Change Q2 & Q4 to IRF9540N
    Add Push Button to start the Due
    Change pinChargeEnable to pinChargeRelay
    [Ardumower.kicad_pcb, charge_pcb.kicad_pcb, charge_pcb.sch]
2021-05-16 Rotate PCB_1 Connector to fit with Main PCB
    [charge_pcb.sch]
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2021-05-17 Improve Q2 and Q4
    [charge_pcb.kicad_pcb, charge_pcb.sch]
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2021-05-17 Remove 24V from PCB
    [Ardumower.kicad_pcb, Ardumower.sch, file609243F3.sch]
2021-05-17 Add 2 new Motor Connectors and Odo
    [Ardumower.kicad_pcb]
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2021-05-21 Board Route
    Board routed and make Gerber Files
    [Ardumower-B_Cu.gbr, Ardumower-B_Mask.gbr, Ardumower-B_Paste.gbr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]
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2021-06-06 PCB ODO Names Changes
    Change ODO LEFT to Right. Create new Schematic PDF. Create New Gerber Files.
    [Ardumower-B_Cu.gbr, Ardumower-B_Mask.gbr, Ardumower-B_Paste.gbr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]
2021-06-06 Delete DUE_PCB_V1.01 directory
    Delete and add Files to 1.00
    [Ardumower.dsn, Ardumower.kicad_pcb, Ardumower.sch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]
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2021-06-06 Delete DUE_PCB_V1.02BER directory
    All in default DUE_PCB
    [Ardumower.dsn, Ardumower.kicad_pcb, Ardumower.sch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]
2021-06-25 Change Q2 and Q4
    [Ardumower.kicad_pcb, Ardumower.kicad_sch, SimpleMainPCB.kicad_pcb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]
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
